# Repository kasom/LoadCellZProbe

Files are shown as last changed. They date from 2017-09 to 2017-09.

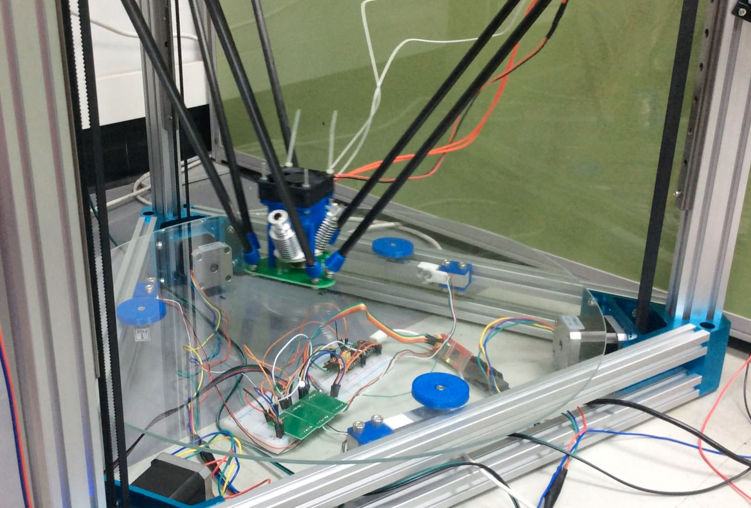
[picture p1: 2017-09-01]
images/testrun.jpg

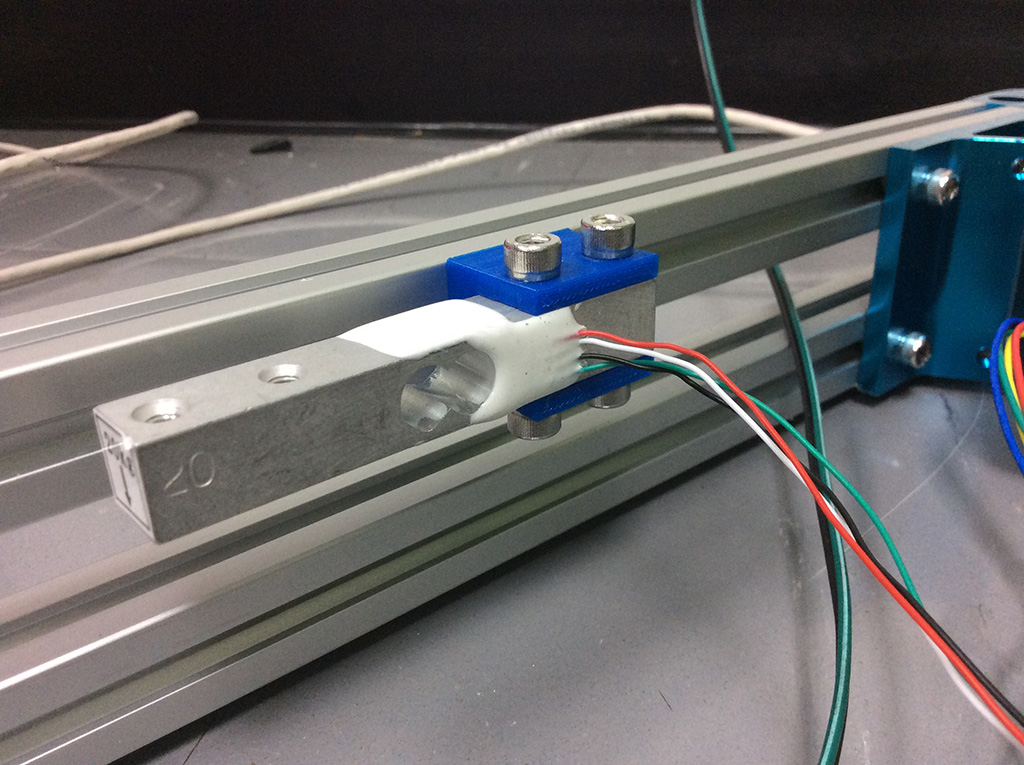
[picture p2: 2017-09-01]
images/mount4.jpg

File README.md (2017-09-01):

# LoadCellZProbe
Under bed load cell Z-probe. It’s somewhat a mixture of [JohnSL's](https://github.com/JohnSL/FSR_Endstop) and [palmer23's](http://forums.reprap.org/read.php?14,605317,737910).

## What’s needed:

- STM32F103C8T6 board. I’m using a “[black pill](http://wiki.stm32duino.com/index.php?title=Black_Pill)”. Any Arduino compatible board could be used, but those * pills board are really cheap. The STM32 is 3.3V matched the Duet board I'm using.
- STLink v2 or USB to TTL (3.3v) adapter to program the board.
- Arduino IDE + STM32duino
- [HX711-multi library](https://github.com/compugician/HX711-multi)
    - Edit HX711-multi.h by removing "HX711MULTI::" from line 49. (It won't compile if you don't remove it)
- 3 load cells. I’m using 5 Kgs load cell.
- 3 HX711 breakout board, [set sampling rate to 80 samples per second](http://www.instructables.com/id/Reprap-Load-Cell-Z-Probe/).
- Printed parts to mount the load cells & support the bed
- Connectors, wires, screws, springs, etc.

## How did it work?

- Load cell output is linear. By using 3 load cell to support the build plate, the output of 3 load cells can be summed and then used to detect force (weight) applied to any point in the build plate. (Detect the nozzle press at any point in the build plate.)
- The firmware collect the load cell's outputs (weight + noise) and use the range of noise as a trigger threshold.

## How to use it?

1. Flash the firmware into the STM32 board. Disconnect all wires.
2. Connect the load cells to the HX711 boards.
3. Connect GND and VCC pin of the HX711 boards to GND and +3V of the STM32 board.
4. Connect all SCK (Clock) pin of the HX711 boads to pin PA7 of the STM32 board.
5. Connect each DT (Data) pin of the HX711 boards to pin PA0, PA1 and PA2.
6. Apply power to the STM32 board.
    1. The blue LED on the STM32 should light up for 10 seconds, indicating the noise learning phase. (It read 80 x 10 samples from every HX711).
    2. When the blue LED is off, indicate the untrigger state.
    3. The blue LED will light up again enought force is applited to the load cell. (A finger push on the tip of load cell should activate it).
7. If all went well, disconnect the power source and then connect pin PB0 to Z probe input of your 3D printer board. (It's active high). After that apply power to the STM32 board and test your new Z-probe!

## Trouble shooting

- The USB of the STM32 board is a virtual serial port, use a USB cable to plug it into your computer.
- Use your terminal program to connect the virtual serial to see the debug information.
- The connection speed doesn't matter, you can use 9600, 115200, etc.
- If you send any character through the terminal, it will trigger the noise learning phase.
- To enable verbose output mode, connect pin PA9 of the STM32 board to GND.

## Noise read enable pin (PA10)

Connecting the PA10 pin of STM32 board to GND (or send logic low from your 3D printer board) will activate the noise learning phase, similar to when the firmware start or when sending a character through the terminal. Except that it will read at least 80x10 samples, more if you continue to hold the pin low. It's useful if you want to let your 3D printer board control when to read the noise floor. For example, pull the pin low and then move the print head around (but make sure that it won't tuch the build plate) to let the firmware learn about the noise/vibration generated by the steppers.

## Links

- [A thread in RepRap forum](http://forums.reprap.org/read.php?178,784481)

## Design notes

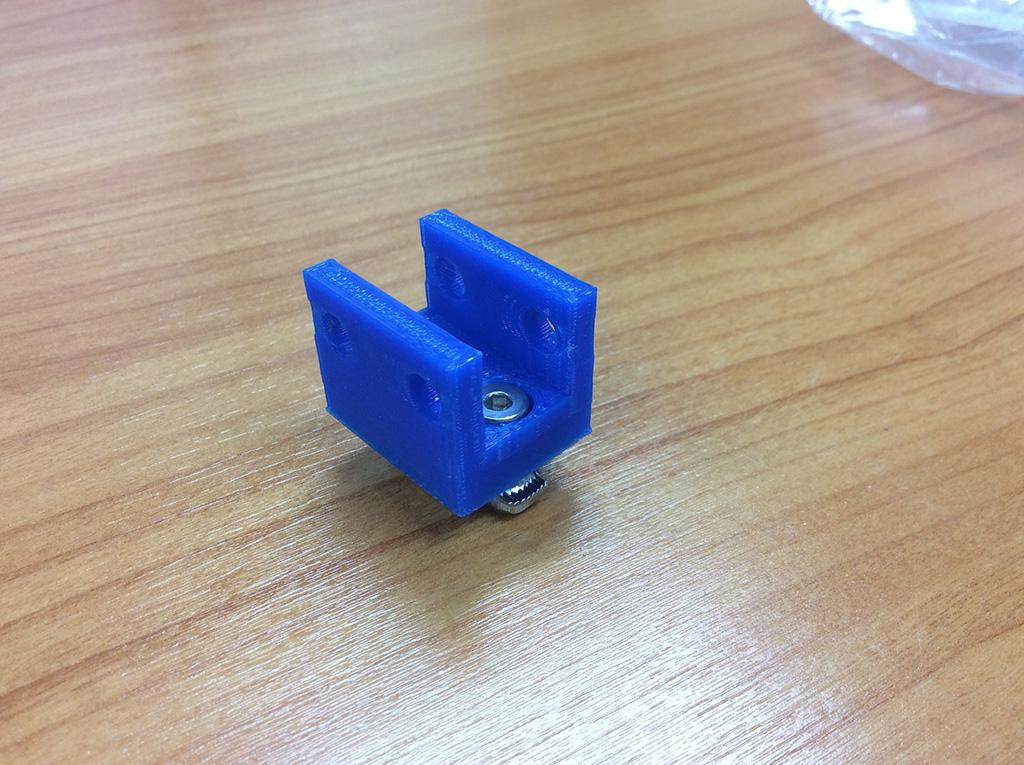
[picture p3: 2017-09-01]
images/mount3.jpg

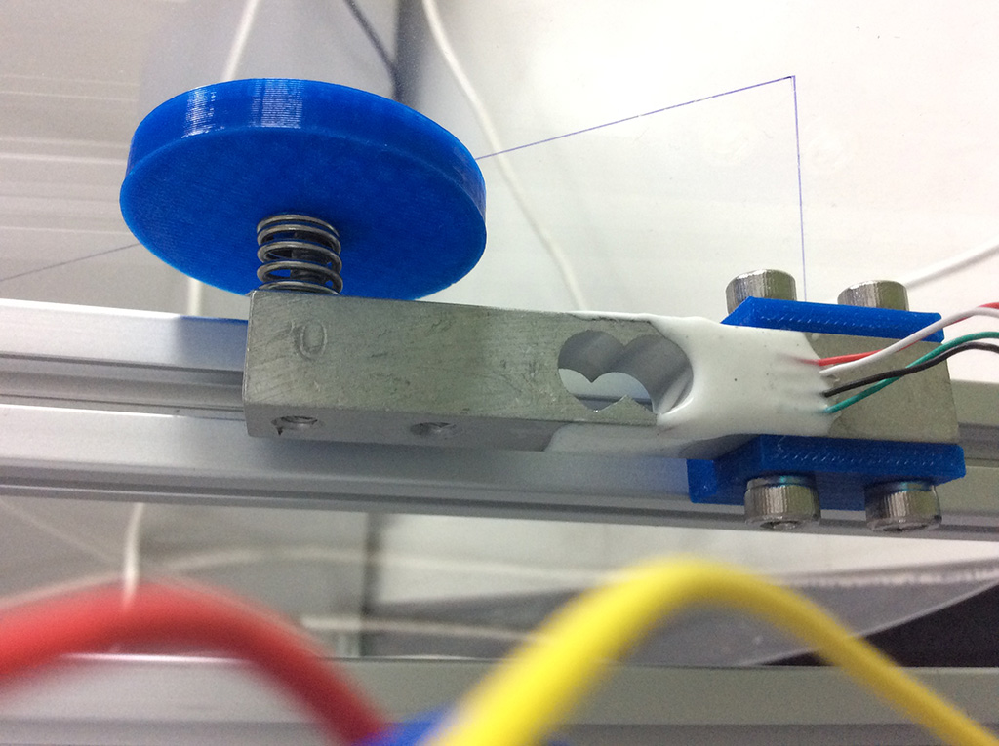
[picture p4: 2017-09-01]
images/mount1.jpg

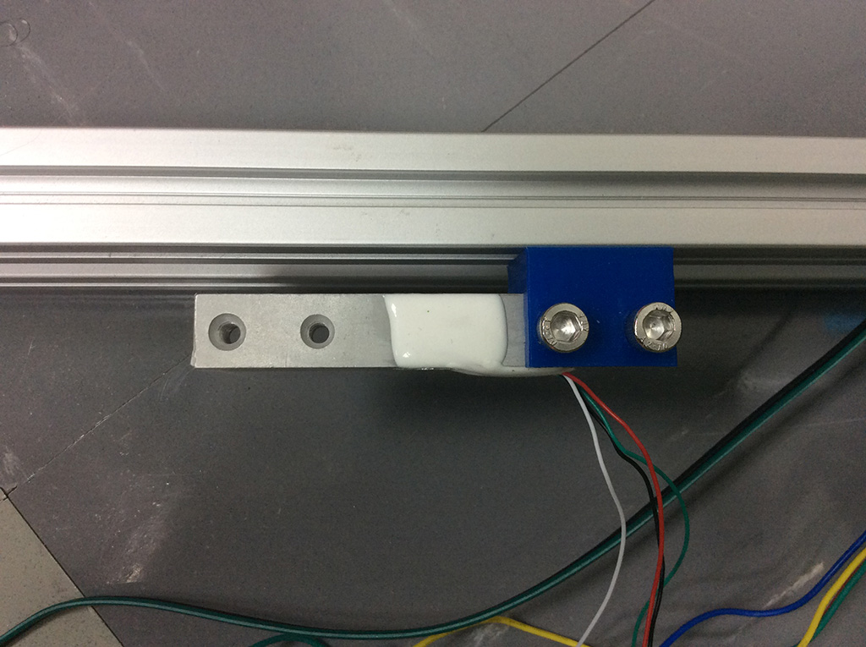
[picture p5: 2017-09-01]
images/mount2.jpg

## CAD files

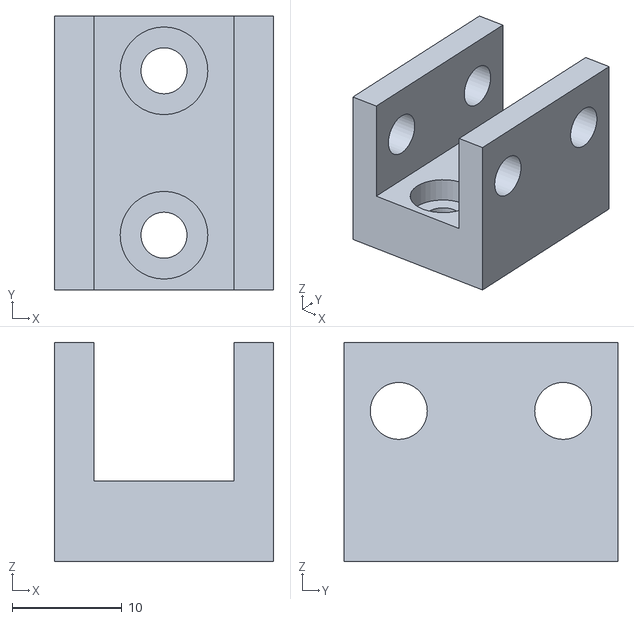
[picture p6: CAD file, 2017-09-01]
3D/loadcell_mount.stl
20.0 x 25.0 x 20.0

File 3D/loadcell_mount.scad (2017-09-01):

aluminium_height=20;
loadcell_size=12.5;
mount_depth=20;
mount_long=25;
mount_loc=15/2;
safety=0.3;
screw_head_thick=3;
screw_head_dia=8;

rotate([0,270,0])
difference() {
    linear_extrude(aluminium_height) square([mount_depth,mount_long],true);

    translate([(mount_depth-loadcell_size)/2,0,(aluminium_height-loadcell_size)/2-safety/2])
        linear_extrude(loadcell_size+safety)
            square([loadcell_size+safety,mount_depth*2+safety],true);
    
    translate([(mount_depth-loadcell_size)/2,mount_loc,-aluminium_height/2])
        linear_extrude(aluminium_height*2+safety) circle(d=5.2,$fn=36);

    translate([(mount_depth-loadcell_size)/2,-mount_loc,-aluminium_height/2])
        linear_extrude(aluminium_height*2) circle(d=5.2,$fn=36);


    translate([-mount_depth,-mount_loc,aluminium_height/2])
        rotate([0,90,0])
            linear_extrude(mount_depth*2)
                circle(d=4.2,$fn=36);

    translate([-mount_depth,mount_loc,aluminium_height/2])
        rotate([0,90,0])
            linear_extrude(mount_depth*2)
                circle(d=4.2,$fn=36);

    translate([(mount_depth-loadcell_size)-mount_depth/2-screw_head_thick,mount_loc,aluminium_height/2])
        rotate([0,90,0])
            linear_extrude(screw_head_thick)
                circle(d=screw_head_dia,$fn=36);

    translate([(mount_depth-loadcell_size)-mount_depth/2-screw_head_thick,-mount_loc,aluminium_height/2])
        rotate([0,90,0])
            linear_extrude(screw_head_thick)
                circle(d=screw_head_dia,$fn=36);
}

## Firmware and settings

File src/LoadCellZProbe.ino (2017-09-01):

/* See: https://github.com/kasom/LoadCellZProbe */

#include "HX711-multi.h"

#define CHANNEL_COUNT 3

// clock pin to the load cell amp
#define HX711_CLK_PIN PA7
// data pins to the load cell amp
#define HX711_DATAL_PINS {PA0,PA1,PA2}

// Active low
#define LED_PIN PB12
// Active high
#define OUTPUT_PIN PB0

// Active low
#define VERBOSE_OUTPUT_ENABLE PA9
// Active low
#define NOISE_READ_ENABLE PA10

#define SAFETY_MARGIN 8
#define MIN_N_NOISE_SAMPLE 80*10

// ******************************************************************

byte DOUTS[CHANNEL_COUNT] = HX711_DATAL_PINS;

long int results[CHANNEL_COUNT];

HX711MULTI scales(CHANNEL_COUNT, DOUTS, HX711_CLK_PIN);

void setOutputActive(bool isActive) {
  if (isActive) {
    digitalWrite(LED_PIN, LOW); // Active low
    digitalWrite(OUTPUT_PIN, HIGH); // Active height
  } else {
    digitalWrite(LED_PIN, HIGH);
    digitalWrite(OUTPUT_PIN, LOW);
  }
}

class ZProbe {
  private:
    long rawAvg[CHANNEL_COUNT];
    long noiseRange;
    int nNoiseSample;

    HX711MULTI scales;

  public:
    ZProbe(HX711MULTI scales):scales(scales) {
      readNoise();
    }
  
    bool isTriggered() {
      long raws[CHANNEL_COUNT];
      long sumAdj=0;
      scales.readRaw(raws);

      bool verboseMode=(digitalRead(VERBOSE_OUTPUT_ENABLE)==0);

      for (int i=0;i<CHANNEL_COUNT;i++) {
          sumAdj+=raws[i]-rawAvg[i];
      }

      long sumDivNoise=sumAdj/noiseRange;
      
      if (verboseMode) {
        Serial.print("RAW\t");
        for (int i=0;i<CHANNEL_COUNT;i++) {
          Serial.print(raws[i]);
          Serial.print("\t");
        }
        Serial.print("ADJ\t");
        for (int i=0;i<CHANNEL_COUNT;i++) {
          Serial.print(raws[i]-rawAvg[i]);
          Serial.print("\t");
        }
        Serial.print("SUM\t");
        Serial.print(sumAdj);
        Serial.print("/Noise\t");
        Serial.println(sumDivNoise);
        
        if (sumDivNoise!=0) {
          Serial.print("Triggered ");
          Serial.println(sumDivNoise);
        }
      }

      return sumDivNoise!=0;
    }

    void readNoise() {
      long long sum[CHANNEL_COUNT];
      long rawsMin[CHANNEL_COUNT];
      long rawsMax[CHANNEL_COUNT];
      long raws[CHANNEL_COUNT];

      setOutputActive(true);

      Serial.println("Reading noise samples...");

      scales.readRaw(raws); // throw away the first reading

      for (int i=0;i<CHANNEL_COUNT;i++) {
        scales.readRaw(raws);
        sum[i]=raws[i];
        rawsMin[i]=raws[i];
        rawsMax[i]=raws[i];
      }

      int noiseSampleCount=0;
      
      for (noiseSampleCount=0;noiseSampleCount<MIN_N_NOISE_SAMPLE-1  || (digitalRead(NOISE_READ_ENABLE)==0);noiseSampleCount++) {
        scales.readRaw(raws);

        for (int i=0;i<CHANNEL_COUNT;i++) {
          if (rawsMin[i]>raws[i]) rawsMin[i]=raws[i];
          if (rawsMax[i]<raws[i]) rawsMax[i]=raws[i];
          sum[i]+=raws[i];
        }
      }

      nNoiseSample=noiseSampleCount+1;

      long sumRange=0;

      noiseRange=0;

      for (int i=0;i<CHANNEL_COUNT;i++) {
        noiseRange+=SAFETY_MARGIN*(rawsMax[i]-rawsMin[i]);
        
        rawAvg[i]=sum[i]/nNoiseSample;
      }

      Serial.print("N Noise Samples: ");
      Serial.println(nNoiseSample);
      
      Serial.print("Noise floor:");
      Serial.print(" range=");
      Serial.println(noiseRange);

      setOutputActive(false);
    }
};

ZProbe *zProbe;

void setup() {
  Serial.begin(115200);
  Serial.flush();

  pinMode(LED_PIN,OUTPUT);
  pinMode(OUTPUT_PIN,OUTPUT);

  pinMode(VERBOSE_OUTPUT_ENABLE,INPUT_PULLUP);
  pinMode(NOISE_READ_ENABLE,INPUT_PULLUP);

  zProbe=new ZProbe(scales);
}

void loop() {

  setOutputActive(zProbe->isTriggered());

  if (digitalRead(NOISE_READ_ENABLE)==0) {
    zProbe->readNoise();
  } else if (Serial.available()>0) {   //on serial data (any data) re-read noise floor
    while (Serial.available()) {
      Serial.read();
    }
    zProbe->readNoise();
  } 
}
